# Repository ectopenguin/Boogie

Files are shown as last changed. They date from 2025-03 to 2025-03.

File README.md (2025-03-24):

# Boogie
Carbon/HEPA filter and sheet cooling in a tiny package!

boogie

It started as a dream... In my tiny printer, I wanted filtration and sheet cooling.
Using parts from other abandoned dreams and amateur but slowly improving CAD skills, this monstrosity was borne into the world.
3628 fans do the work and an MG90s servo makes the fans boogie!
Best of all, no need to disassemble your painstakingly squared frame, as I've created an M2 drop in nut holder to secure it all.

Enjoy the Boogie!

<br/><br/>

**A Few Notes:**
* Hex-zero bumps out the panels 3mm from a stock v0. This extra space is necessary for the fan rotation.
* I use SlideSwipe for my bed probe. I have not tested this with ZeroClick.
* I built my Hex-zero awhile ago. If you've built yours more recently, some things may have changed. Such as:
   * I'm using the standard DragonBurner (not the Hex-Zero varient which I believe is lifted a few mm).
   * I'm using the standard bed, not the newer manta ray. Not sure of clearance with the newer version of the bed.
* Extreme left tilting of bed will likely cause some contact between bed and Boogie.
* When in fan mode, you'll have to limit the low end of x to about -5 or maybe -4 to prevent nozzle from colliding.
    * Can either limit this in config, or can make sure that all activities involving this area (maybe bed probing etc) are done prior to engaging fan mode.

<br/><br/>

**Bill of Materials (BOM)**
| Qty | Item | Notes |
| --- | --- | --- |
| 8 | 3x6 magnets |
| 12 | M2 nuts |
| 2 | M2x4 SHCS | To secure the servo horn. Can likely use 6mm if you use a spacer |
| 4 | M2x6 SHCS | To secure bottom mounts to frame |
| 6 | M2x8 SHCS | To secure top mounts to frame and servo to top rear mount |
| 1 | M5x10 BHCS | For the front mount |
| 8 | M3x35 BHCS | 32-33mm would be better, but I've got no bolt cutters |
| 8 | M3 nuts | For use as spacer, no need if able to acquire shorter screws |
| 8 | M3x5x4 heat set inserts | For the fan mount to secure fans |
| 1 | MR85zz bearing | Press fit into the fan mount. The M5 screw from front mount goes through here |
| 1 | MG90s servo with horn |
| 2 | 36mm x 28 mm fans | I'm using Delta FFB03612EHNYCL |
| 1 | Robot Vacuum Filter | Mine measure 130mm long x 40mm wide x 8mm tall which I've cut to length |
| ~80mm | 6mm wide x 1mm thick foam tape | Goes on the rear of filter (left on the photo) to improve fan seal to filter |
| Misc | Wiring, possibly a buck converter depending on your setup |

<br/><br/>
<br/><br/>
This work is licensed under a <a href="http://creativecommons.org/licenses/by-nc-sa/4.0/" rel="nofollow">Creative Commons Attribution-NonCommercial-ShareAlike 4.0 International License</a>

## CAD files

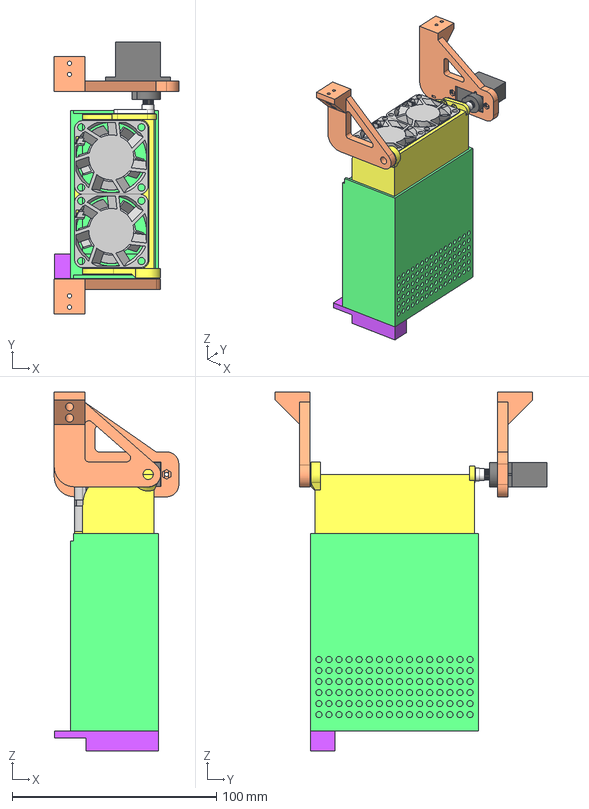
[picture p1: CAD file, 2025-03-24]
CAD/Boogie.step
61.0 x 133.0 x 175.8 mm
MG90S horn v1
FFB036XX-XXN_FRAME_1 x 2
PRT0001_1 x 2
servo motor (mg90s) v1
Filter
Top Mount
Bottom Mount adjustable

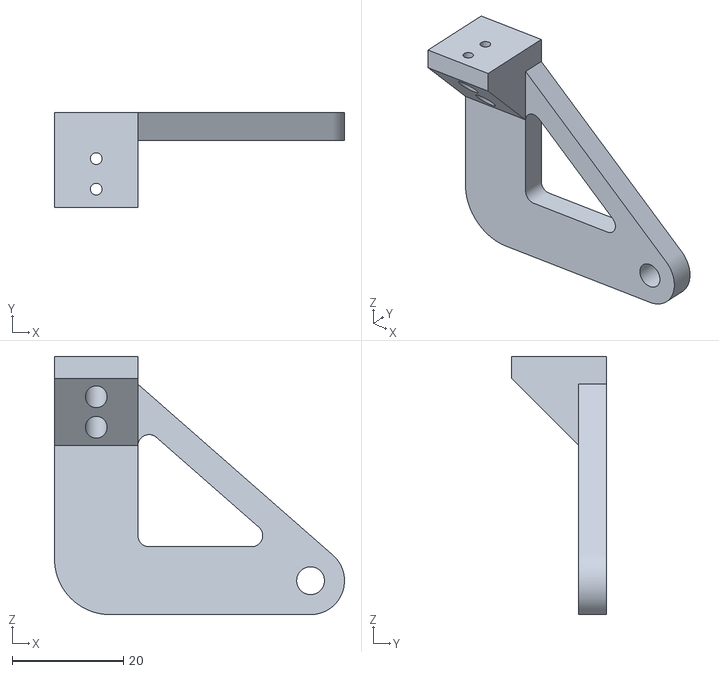
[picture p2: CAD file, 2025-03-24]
STLs/top mount front.stl
52.1 x 17.0 x 46.4

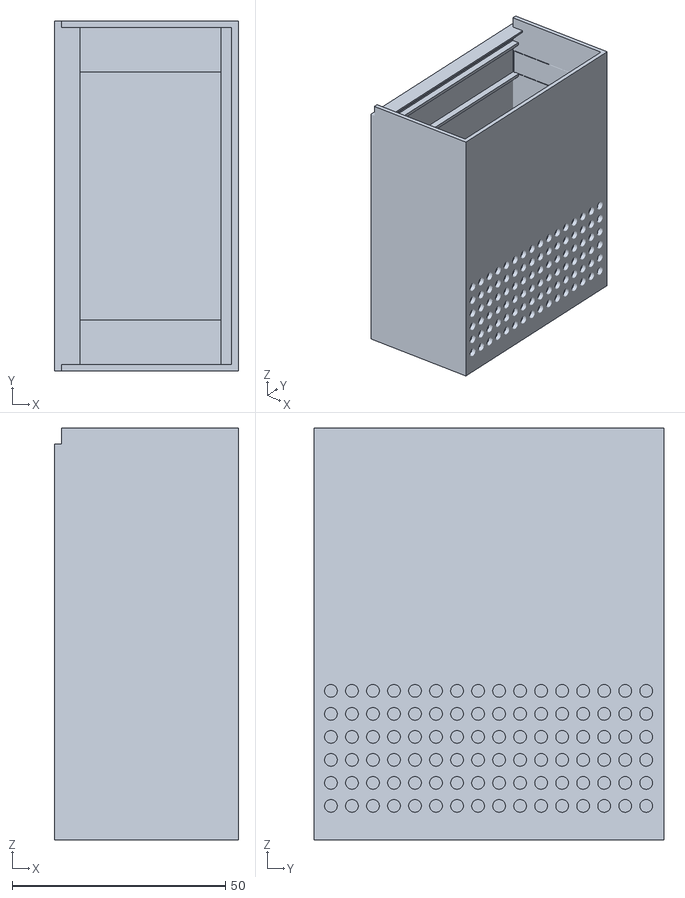
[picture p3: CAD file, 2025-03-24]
STLs/filter.stl
43.2 x 82.2 x 96.7

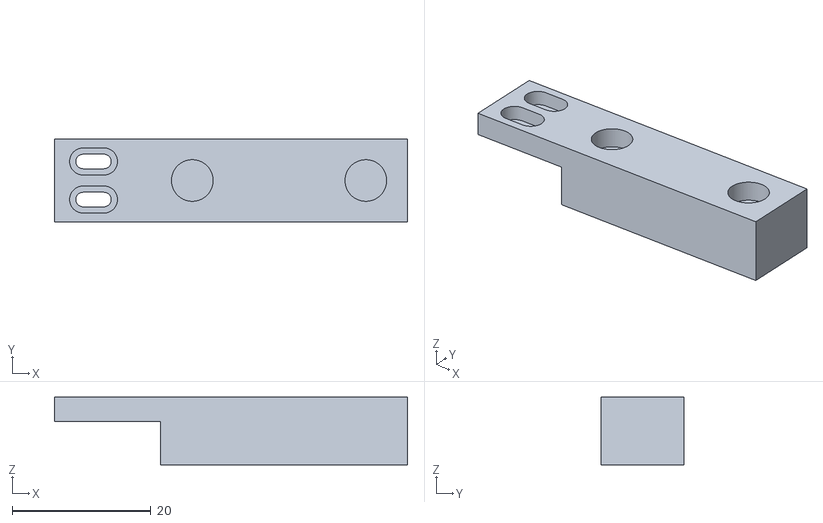
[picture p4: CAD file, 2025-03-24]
STLs/bottom mount x2.stl
50.8 x 12.0 x 9.79

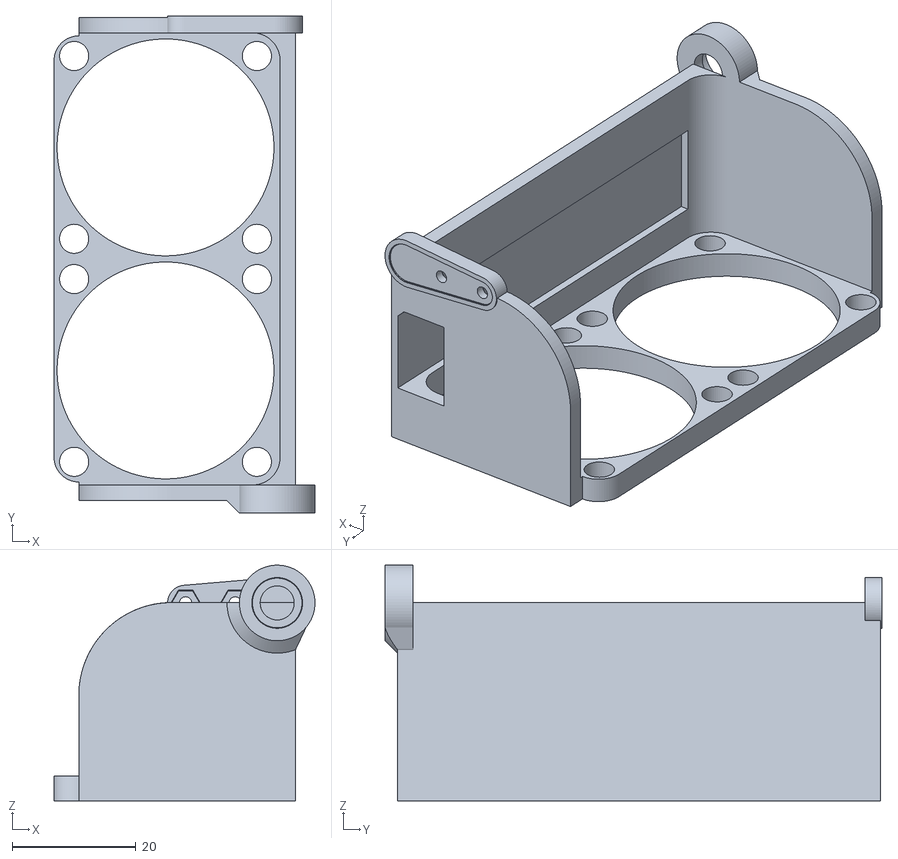
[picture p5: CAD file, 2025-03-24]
STLs/fan mount.stl
42.1 x 80.2 x 38.0

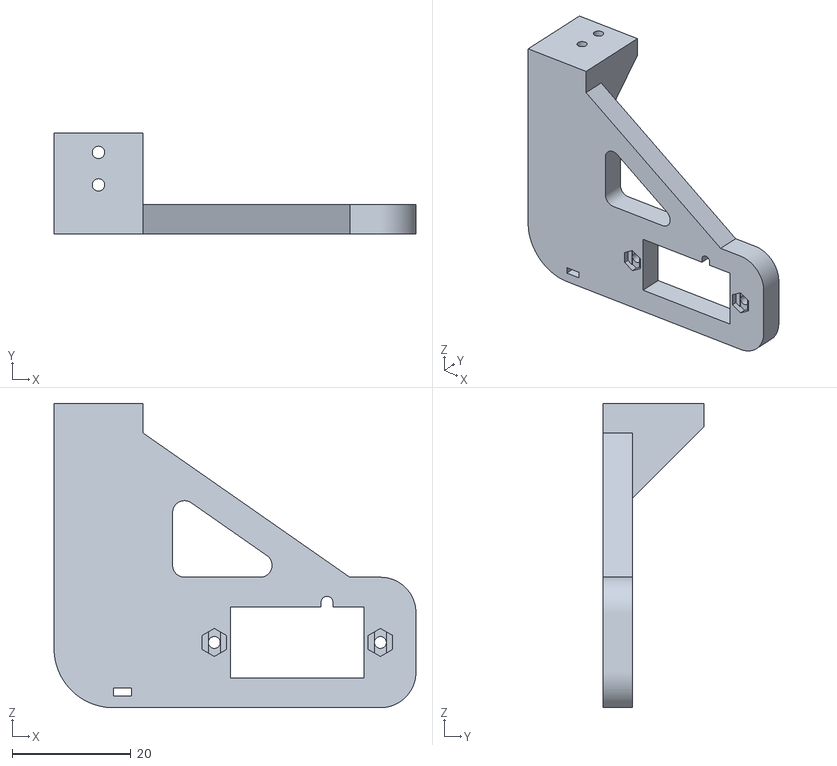
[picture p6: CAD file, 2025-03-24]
STLs/top mount rear.stl
61.0 x 17.0 x 51.3

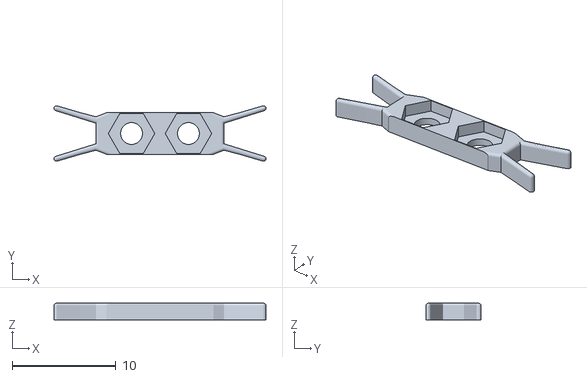
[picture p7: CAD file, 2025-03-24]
STLs/double m2 nut holder x4.stl
20.4 x 5.34 x 1.60

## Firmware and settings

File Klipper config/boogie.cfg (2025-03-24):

[servo boogyServo]
pin: #Add your pin here
maximum_servo_angle: 180
minimum_pulse_width: 0.000700
maximum_pulse_width: 0.002150

[fan_generic boogie_fan]
pin: expander: #Add your pin here
kick_start_time: 0.5

[gcode_macro BOOGIE_FAN]
gcode:
    SET_SERVO SERVO=boogyServo ANGLE=30 #Adjust as needed
    G4 P500 # wait
    
[gcode_macro BOOGIE_FILTER]
gcode:
    SET_SERVO SERVO=boogyServo ANGLE=160 #Adjust as needed
    G4 P500 # wait
